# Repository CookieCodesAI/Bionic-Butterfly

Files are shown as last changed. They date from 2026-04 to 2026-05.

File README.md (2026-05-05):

# Bionic-Butterfly
A butterfly-like drone that can be manually controlled from your computer.

## Why I made this project
For a while now, I've been wanted to create bigger hardware projects than the ones that I had been making previously. I wanted to make an aesthetic project that would make me go beyond my limits. Making a drone was the first idea that came to mind, and with the help of my Instagram feed, I got inspired to make a butterfly drone, leading to the creation of this project!

### 3D model of whole project
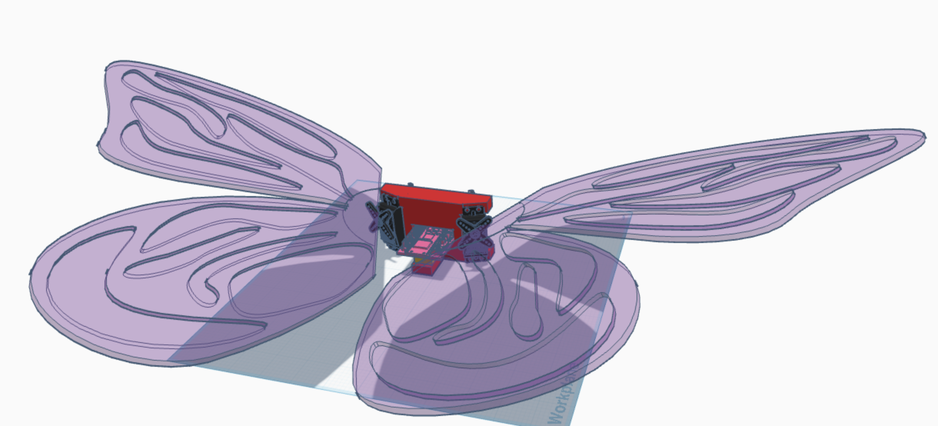
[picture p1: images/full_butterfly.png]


The wings will be made with flower paper and carbon fiber to make sure that they don't weigh too much. Additionally, the wings will be connected to the servo horns with a connector that I will make and mold to make sure that it fits perfectly.  

### 3D model of main body with Servos and Raspberry Pi Pico
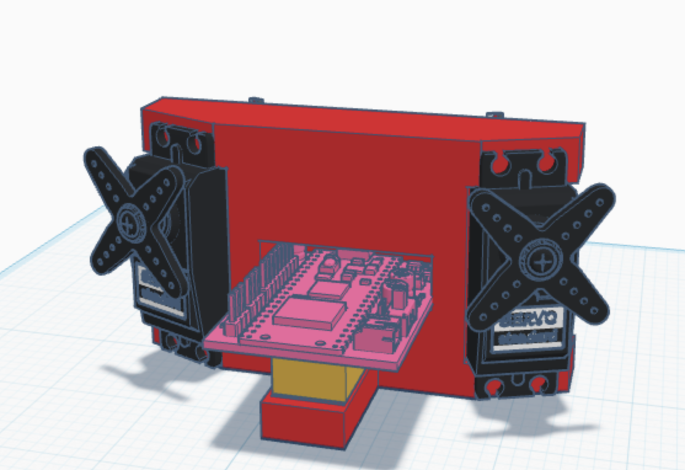
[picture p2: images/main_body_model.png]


The PCB will be able to fit in the gap in the middle of the body. The servos will be placed on the angled sides of the main body and the wires will be connected as shown in the wiring diagram. The 2S LiPo battery is the yellow rectangle that was measured with the dimensions of the LiPo battery in my BOM. 

### Wiring Diagram
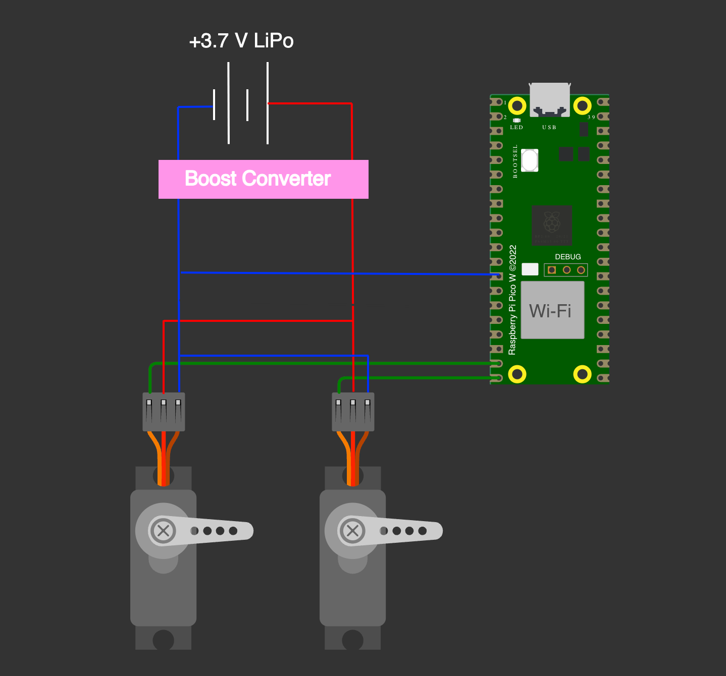
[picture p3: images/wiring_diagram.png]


### Schematics
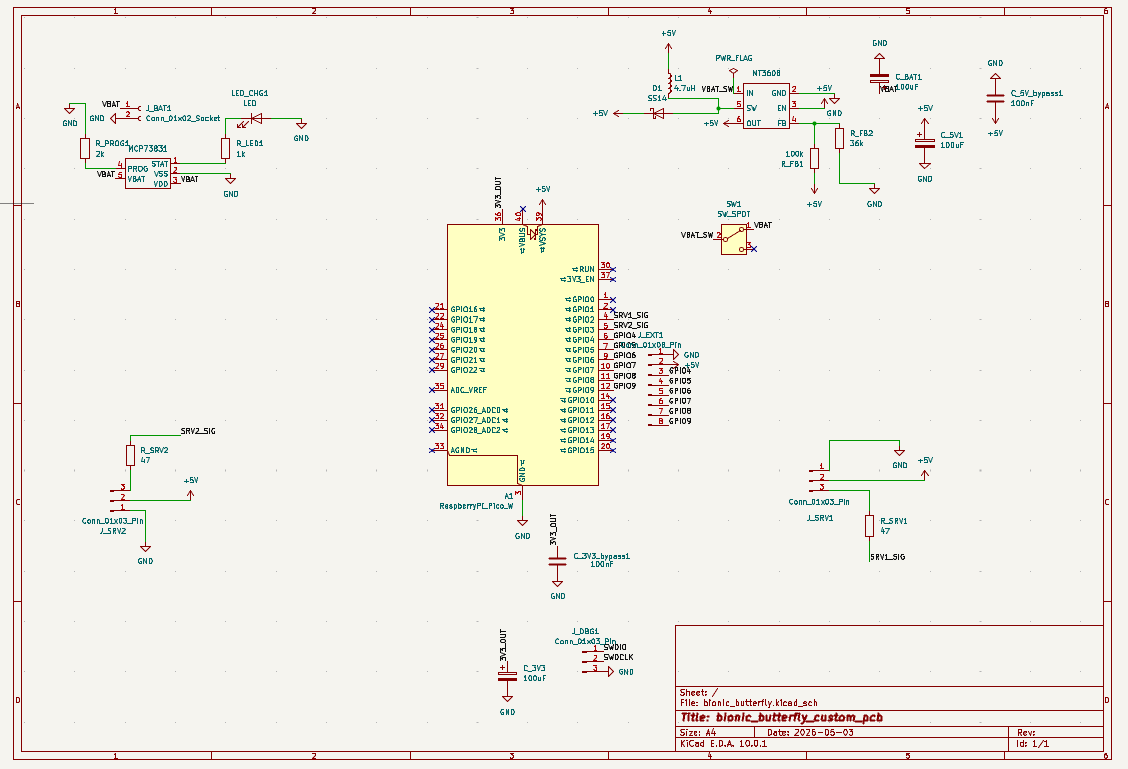
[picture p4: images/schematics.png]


### Custom PCB
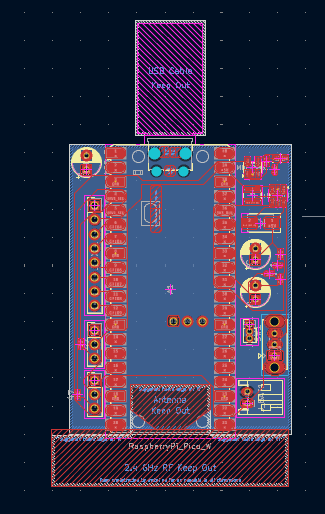
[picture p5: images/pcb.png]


- Boost Converter 
- LiPo Battery Charger 
- LiPo Battery Port
- Raspberry Pi Pico W
- Servo Header Pins for Easy Connection

### BOM
|Name |Quantity|Link |Total Cost|Distributor|Purpose |Footprint |Value |
|---|---|---|---|---|---|---|---|
|PTK 7462W |2 |https://www.amazon.com/7462W-Waterproof-Servo-Motor-Metal/dp/B0FS6RFS5T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 |27.54 |Amazon |Motors for the wings | | |
|2s LiPo Battery |1 |https://www.amazon.com/Tattu-300mAh-7-6V-Battery-JST-PHR/dp/B097BVFYLX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 |9.99 |Amazon |Power for microcontroller and motors | | |
|Custom PCB |5 |https://cart.jlcpcb.com/quote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 |2 |JCLPCB |Manufacturing PCB for custom microcontroller | | |
|A1 |1 |https://www.adafruit.com/product/5526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 |6 |Adafruit |Microcontroller |Module:RaspberryPi_Pico_W_SMD_HandSolder |RaspberryPi_Pico_W|
|C_3V3,C_BAT1 |2 |https://www.digikey.com/en/products/detail/w%C3%BCrth-elektronik/860020473008/5727062 |0.26 |DigiKey |PCB component |Capacitor_THT:CP_Radial_D5.0mm_P2.50mm |100uF |
|C_3V3_bypass1,C_5V_bypass1|2 |https://www.digikey.com/en/products/detail/samsung-electro-mechanics/CL05B104KP5VPNC/20498482 |0.2 |DigiKey |PCB component |Capacitor_SMD:C_0402_1005Metric |100nF |
|C_5V1 |1 |https://www.digikey.com/en/products/detail/kemet/ESK107M025AC3AA/2712507 |0.2 |DigiKey |PCB component |Capacitor_THT:CP_Radial_D5.0mm_P2.00mm |100uF |
|D1 |1 |http://digikey.com/en/products/detail/onsemi/SS14/965474 |0.44 |DigiKey |PCB component |Diode_SMD:D_SMA |SS14 |
|J_BAT1 |1 |https://www.digikey.com/en/products/detail/jst-sales-america-inc/S2B-PH-K-S/926626 |0.11 |DigiKey |PCB component |Connector_JST:JST_PH_S2B-PH-K_1x02_P2.00mm_Horizontal |Conn_01x02_Socket |
|J_DBG1 |1 |https://www.digikey.com/en/products/detail/sullins-connector-solutions/GRPB031VWVN-RC/1786439 |0.21 |DigiKey |PCB component |Connector_PinHeader_1.27mm:PinHeader_1x03_P1.27mm_Vertical|Conn_01x03_Pin |
|J_EXT1 |1 |https://www.digikey.com/en/products/detail/w%C3%BCrth-elektronik/61300811121/4846839 |0.4 |DigiKey |PCB component |Connector_PinHeader_2.54mm:PinHeader_1x08_P2.54mm_Vertical|Conn_01x08_Pin |
|J_SRV1,J_SRV2 |2 |https://www.digikey.com/en/products/detail/w%C3%BCrth-elektronik/61300311121/4846825 |0.26 |DigiKey |PCB component |Connector_PinHeader_2.54mm:PinHeader_1x03_P2.54mm_Vertical|Conn_01x03_Pin |
|L1 |1 |https://www.digikey.com/en/products/detail/taiyo-yuden/LCXND3030QKT4R7MNG/22251951 |0.27 |DigiKey |PCB component |Inductor_SMD:L_Taiyo-Yuden_NR-30xx |4.7uH |
|LED_CHG1 |1 |https://www.digikey.com/en/products/detail/sunled/XZFRA53FVC-1/28246155 |0.86 |DigiKey |PCB component |LED_SMD:LED_0603_1608Metric |LED |
|MCP73831 |1 |https://www.digikey.com/en/products/detail/microchip-technology/MCP73831T-2ACI-OT/964301 |0.76 |DigiKey |PCB component |Package_TO_SOT_SMD:SOT-23-5 | |
|MT3608 |1 |https://www.lcsc.com/product-detail/C84817.html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 |0.79 |LCSC |PCB component |Package_TO_SOT_SMD:SOT-23-6 | |
|R_FB1 |1 |https://www.digikey.com/en/products/detail/yageo/RC0402FR-07100KL/726526 |0.1 |DigiKey |PCB component |Resistor_SMD:R_0402_1005Metric |100k |
|R_FB2 |1 |https://www.digikey.com/en/products/detail/yageo/RC0402FR-0736KL/726598 |0.1 |DigiKey |PCB component |Resistor_SMD:R_0402_1005Metric |36k |
|R_LED1 |1 |https://www.digikey.com/en/products/detail/yageo/RC0402FR-071KL/726513 |0.1 |DigiKey |PCB component |Resistor_SMD:R_0402_1005Metric |1k |
|R_PROG1 |1 |https://www.digikey.com/en/products/detail/yageo/RC0402FR-072KL/2827565 |0.1 |DigiKey |PCB component |Resistor_SMD:R_0402_1005Metric |2k |
|R_SRV1,R_SRV2 |2 |https://www.digikey.com/en/products/detail/yageo/RC0402FR-0747RL/2827566 |0.2 |DigiKey |PCB component |Resistor_SMD:R_0402_1005Metric |47 |
|SW1 |1 |https://www.digikey.com/en/products/detail/c-k/OS102011MS2QN1/411602 |0.73 |DigiKey |PCB component |Button_Switch_THT:SW_Slide_SPDT_Straight_CK_OS102011MS2Q  |SW_SPDT |

### Total materials cost: $51.62

### Materials that are needed that I did not include in the BOM (Since I already have them)
- 1.00 mm carbon fiber
- Some type of thin flower/kite paper

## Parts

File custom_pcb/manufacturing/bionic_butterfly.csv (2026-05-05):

Reference | Qty | Value | DNP | Exclude from BOM | Exclude from Board | Footprint | Datasheet
A1 | 1 | RaspberryPi_Pico_W |  |  |  | Module:RaspberryPi_Pico_W_SMD_HandSolder | https://datasheets.raspberrypi.com/picow/pico-w-datasheet.pdf
C_3V3,C_BAT1 | 2 | 100uF |  |  |  | Capacitor_THT:CP_Radial_D5.0mm_P2.50mm
C_3V3_bypass1,C_5V_bypass1 | 2 | 100nF |  |  |  | Capacitor_SMD:C_0402_1005Metric
C_5V1 | 1 | 100uF |  |  |  | Capacitor_THT:CP_Radial_D5.0mm_P2.00mm
D1 | 1 | SS14 |  |  |  | Diode_SMD:D_SMA
J_BAT1 | 1 | Conn_01x02_Socket |  |  |  | Connector_JST:JST_PH_S2B-PH-K_1x02_P2.00mm_Horizontal
J_DBG1 | 1 | Conn_01x03_Pin |  |  |  | Connector_PinHeader_1.27mm:PinHeader_1x03_P1.27mm_Vertical
J_EXT1 | 1 | Conn_01x08_Pin |  |  |  | Connector_PinHeader_2.54mm:PinHeader_1x08_P2.54mm_Vertical
J_SRV1,J_SRV2 | 2 | Conn_01x03_Pin |  |  |  | Connector_PinHeader_2.54mm:PinHeader_1x03_P2.54mm_Vertical
L1 | 1 | 4.7uH |  |  |  | Inductor_SMD:L_Taiyo-Yuden_NR-30xx
LED_CHG1 | 1 | LED |  |  |  | LED_SMD:LED_0603_1608Metric
MCP73831 | 1 |  |  |  |  | Package_TO_SOT_SMD:SOT-23-5
MT3608 | 1 |  |  |  |  | Package_TO_SOT_SMD:SOT-23-6
R_FB1 | 1 | 100k |  |  |  | Resistor_SMD:R_0402_1005Metric
R_FB2 | 1 | 36k |  |  |  | Resistor_SMD:R_0402_1005Metric
R_LED1 | 1 | 1k |  |  |  | Resistor_SMD:R_0402_1005Metric
R_PROG1 | 1 | 2k |  |  |  | Resistor_SMD:R_0402_1005Metric
R_SRV1,R_SRV2 | 2 | 47 |  |  |  | Resistor_SMD:R_0402_1005Metric
SW1 | 1 | SW_SPDT |  |  |  | Button_Switch_THT:SW_Slide_SPDT_Straight_CK_OS102011MS2Q

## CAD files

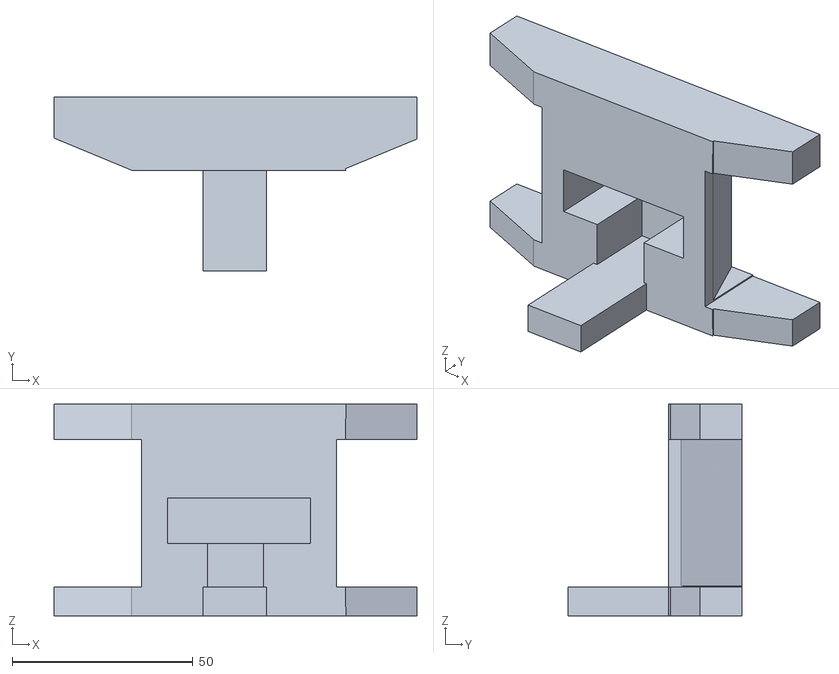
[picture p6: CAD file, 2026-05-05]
3d-models/bionic_butterfly_3d_print.stl
100.4 x 48.0 x 58.6

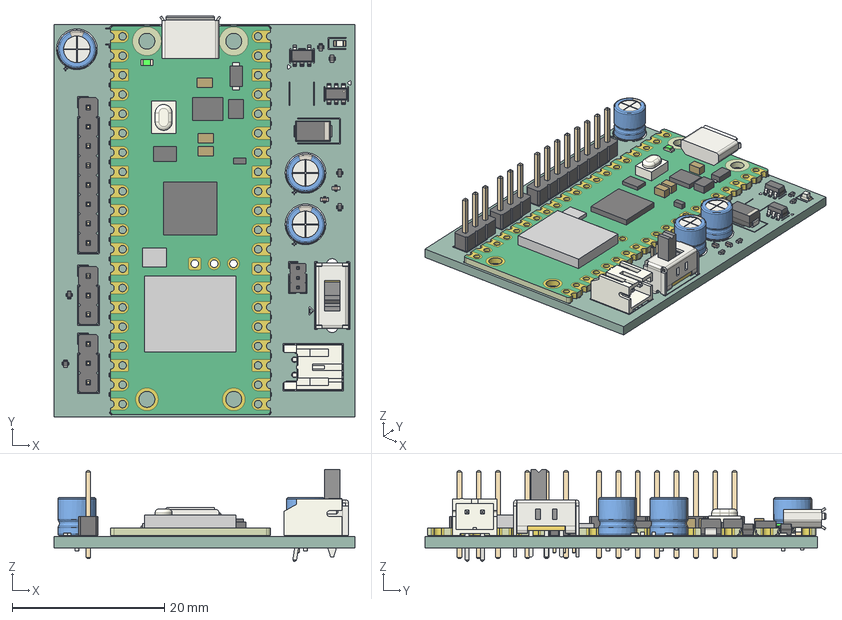
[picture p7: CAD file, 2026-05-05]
3d-models/bionic_butterfly_custom_pcb.step
39.5 x 52.6 x 12.1 mm
SW_Slide_SPDT_Straight_CK_OS102011MS2Q
JST_PH_S2B-PH-K_1x02_P2.00mm_Horizontal
PinHeader_1x03_P2.54mm_Vertical x 2
R_0402_1005Metric x 6
RaspberryPi_Pico_W_Module_KiCad
CP_Radial_D5.0mm_P2.50mm x 2
PinHeader_1x08_P2.54mm_Vertical
C_0402_1005Metric x 2
SOT-23-5
LED_0603_1608Metric
SOT-23-6
D_SMA
CP_Radial_D5.0mm_P2.00mm
PinHeader_1x03_P1.27mm_Vertical
bionic_butterfly_silkscreen
bionic_butterfly_PCB

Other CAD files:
3d-models/bionic_butterfly_main_body.step
3d-models/bionic-butterfly_full_model.step
3d-models/bionic_butterfly_main_body.f3d

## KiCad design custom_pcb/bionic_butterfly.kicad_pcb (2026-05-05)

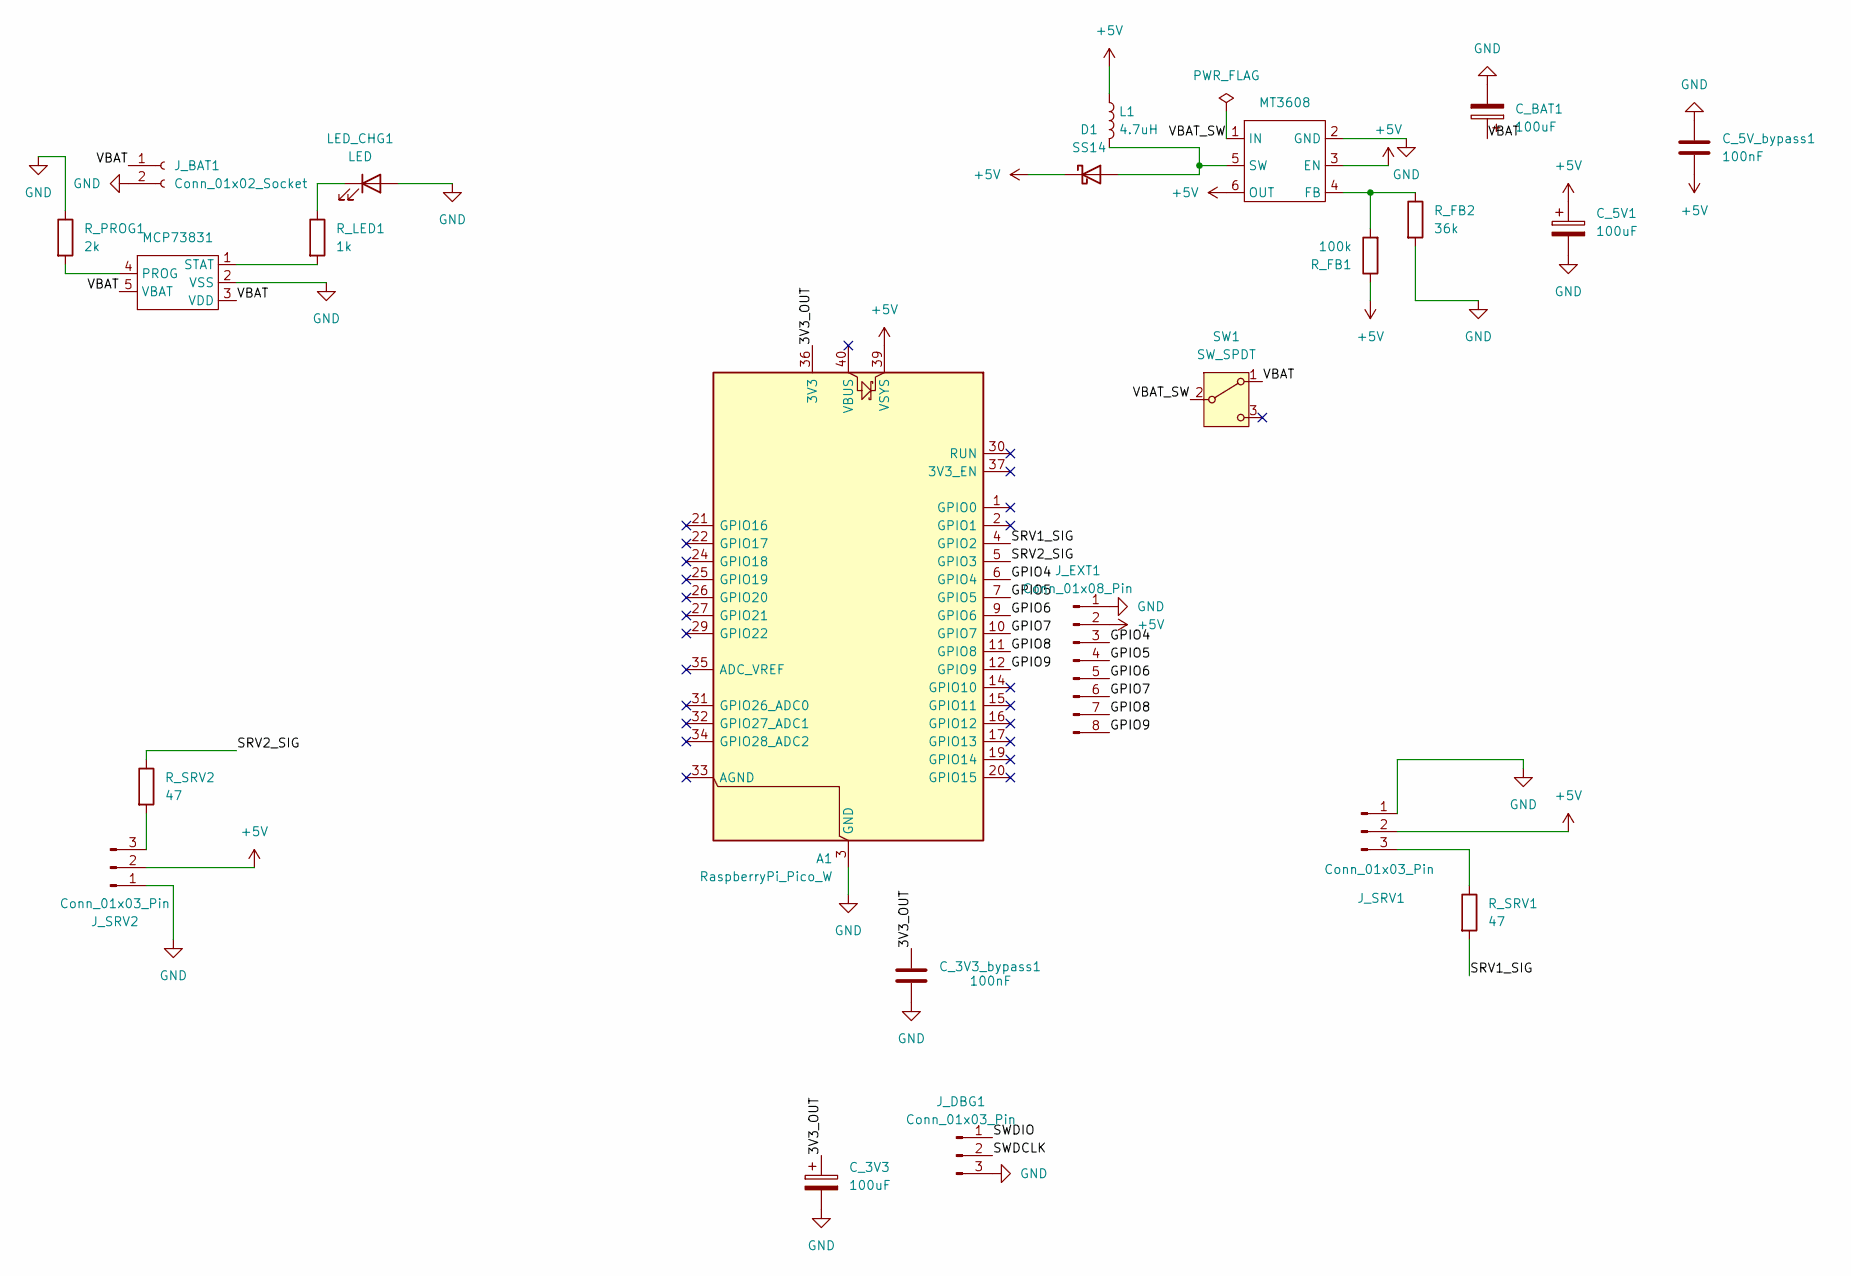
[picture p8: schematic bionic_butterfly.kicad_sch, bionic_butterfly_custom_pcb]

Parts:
A1: RaspberryPi_Pico_W; RaspberryPi_Pico_W_SMD_HandSolder
C_3V3: 100uF; CP_Radial_D5.0mm_P2.50mm
C_3V3_bypass1, C_5V_bypass1: 100nF; C_0402_1005Metric
C_5V1: 100uF; CP_Radial_D5.0mm_P2.00mm
C_BAT1: 100uF; CP_Radial_D5.0mm_P2.50mm
D1: SS14; D_SMA
J_BAT1: Conn_01x02_Socket; JST_PH_S2B-PH-K_1x02_P2.00mm_Horizontal
J_DBG1: Conn_01x03_Pin; PinHeader_1x03_P1.27mm_Vertical
J_EXT1: Conn_01x08_Pin; PinHeader_1x08_P2.54mm_Vertical
J_SRV1, J_SRV2: Conn_01x03_Pin; PinHeader_1x03_P2.54mm_Vertical
L1: 4.7uH; L_Taiyo-Yuden_NR-30xx
LED_CHG1: LED; LED_0603_1608Metric
MCP73831: SOT-23-5
MT3608: SOT-23-6
R_FB1: 100k; R_0402_1005Metric
R_FB2: 36k; R_0402_1005Metric
R_LED1: 1k; R_0402_1005Metric
R_PROG1: 2k; R_0402_1005Metric
R_SRV1, R_SRV2: 47; R_0402_1005Metric
SW1: SW_SPDT; SW_Slide_SPDT_Straight_CK_OS102011MS2Q

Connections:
+5V: A1.39 (VSYS), C_5V1.1, C_5V_bypass1.2, D1.1 (K), J_EXT1.2, J_SRV1.2, J_SRV2.2, L1.1, MT3608.3 (EN), MT3608.6 (OUT), R_FB1.1
/3V3_OUT: A1.36 (3V3), C_3V3.1, C_3V3_bypass1.1
/GPIO4: A1.6 (GPIO4), J_EXT1.3
/GPIO5: A1.7 (GPIO5), J_EXT1.4
/GPIO6: A1.9 (GPIO6), J_EXT1.5
/GPIO7: A1.10 (GPIO7), J_EXT1.6
/GPIO8: A1.11 (GPIO8), J_EXT1.7
/GPIO9: A1.12 (GPIO9), J_EXT1.8
/SRV1_SIG: A1.4 (GPIO2), R_SRV1.2
/SRV2_SIG: A1.5 (GPIO3), R_SRV2.1
/SWDCLK: J_DBG1.2
/SWDIO: J_DBG1.1
/VBAT: C_BAT1.1, J_BAT1.1, MCP73831.3 (VDD), MCP73831.5 (VBAT), SW1.1 (A)
/VBAT_SW: MT3608.1 (IN), SW1.2 (B)
GND: A1.3 (GND), A1.8 (GND), A1.13 (GND), A1.18 (GND), A1.23 (GND), A1.28 (GND), A1.38 (GND), C_3V3.2, C_3V3_bypass1.2, C_5V1.2, C_5V_bypass1.1, C_BAT1.2, J_BAT1.2, J_DBG1.3, J_EXT1.1, J_SRV1.1, J_SRV2.1, LED_CHG1.2 (A), MCP73831.2 (VSS), MT3608.2 (GND), R_FB2.2, R_PROG1.1
unnamed: D1.2 (A), L1.2, MT3608.5 (SW)
unnamed: J_SRV1.3, R_SRV1.1
unnamed: J_SRV2.3, R_SRV2.2
unnamed: LED_CHG1.1 (K), R_LED1.1
unnamed: MCP73831.4 (PROG), R_PROG1.2
unnamed: MCP73831.1 (STAT), R_LED1.2
unnamed: MT3608.4 (FB), R_FB1.2, R_FB2.1

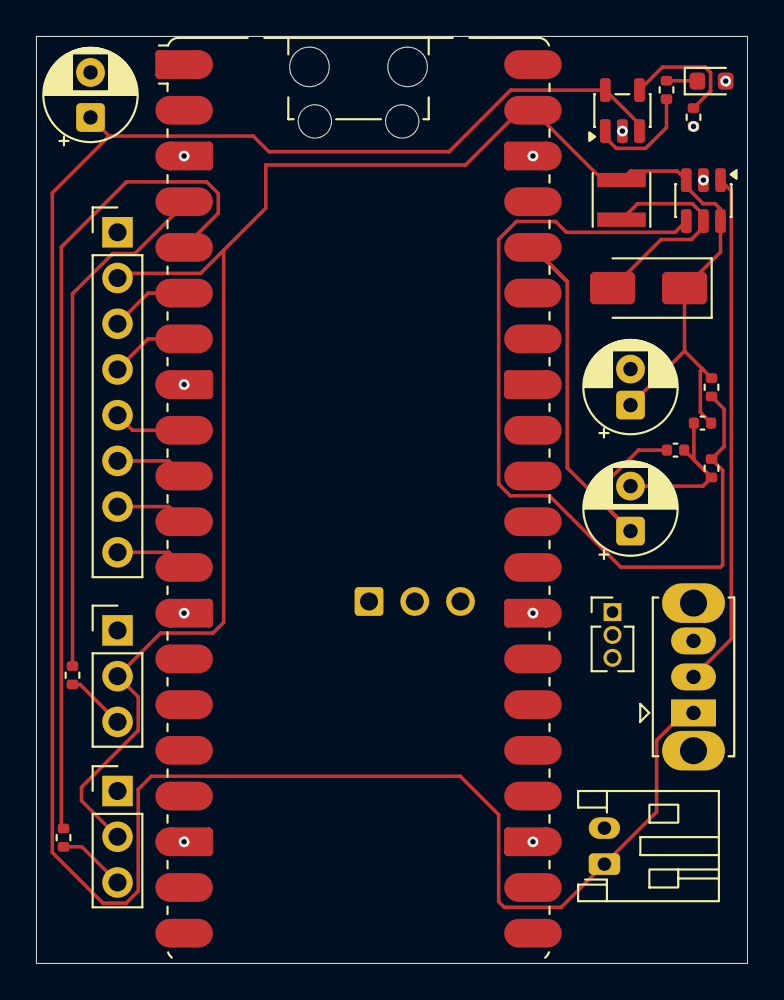
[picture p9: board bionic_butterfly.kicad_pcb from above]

Board: 2 copper layers, 39.5 x 51.5 mm, 23 parts (0 on the bottom side), 20 nets.

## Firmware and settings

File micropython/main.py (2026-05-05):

from machine import Pin, PWM
import time

r_servo = PWM(Pin(2))
l_servo = PWM(Pin(3))

r_servo.freq(50)
l_servo.freq(50)

#function to set the angle of the servos
def set_angle(servo, angle):
    angle = max(0,min(180, angle))
    duty = int (1638 + (angle/180) * (8192-1638))
    servo.duty_u16(duty)

#The actual speed function will be controlled using an html/js page hosted on the wifi so that the pico can access it
#But for the time being, I will just code a basic speed function
def speed_dps(speed):
    return 5+(speed-1)*15

#Takes the current angle and then moves it to the target angle and returns the target angle as the new current angle
#Moves based on the calculated step from the sleep time and the speed from speed_dps()
def move(current, target, servo, dps):
    sleep_time = 0.02
    step = dps * sleep_time
    while abs(current-target)> step:
        if current < target:
            current+=step
        else:
            current-=step
        set_angle(servo, current)
        time.sleep(sleep_time)
    set_angle(servo,target)
    return target

curr_r = 0
curr_l = 180
speed = int(input("Enter a speed from 1-10"))
dps = speed_dps(speed)

while True:
    #servo horns will be in their respective positions that will allow one to go 
    #from 0 degrees to 90 degrees and one from 90 degrees to 180 degrees
    curr_r = move(curr_r,0, r_servo, dps)
    curr_l = move(curr_l,180, l_servo, dps)

    time.sleep(0.3)

    curr_r = move(curr_r,180, r_servo, dps)
    curr_l = move(curr_l,0, l_servo, dps)

    time.sleep(0.3)

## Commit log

2026-04-22 added 3D model files
    [Bionic Butterfly Servo Holder.step, Bionic Butterfly Servo Holder.stl, Full-CAD-Model.step]
2026-04-26 added new images and new 3d-models
    [Bionic Butterfly Servo Holder.step, Bionic Butterfly Servo Holder.stl, Full-CAD-Model.step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]
2026-05-05 edited hardware and cad and added BOM
    [Bionic_Butterfly_BOM.csv, bionic-butterfly_full_model.step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]
